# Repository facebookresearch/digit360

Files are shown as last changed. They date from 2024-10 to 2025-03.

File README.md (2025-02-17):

# Digit 360
##### Unlocking new capabilities, and enabling future research on the nature of touch.

<p align="center">
<sub>Mike Lambeta, Tingfan Wu,
Ali Sengül,
Victoria Rose Most,
Nolan Black,
Kevin Sawyer,
Romeo Mercado,
Haozhi Qi,
Chaithanya Krishna Bodduluri,
Alexander Sohn,
Byron Taylor,
Norb Tydingco,
Gregg Kammerer,
Dave Stroud,
Jake Khatha,
Kurt Jenkins,
Kyle Most,
Neal Stein,
Ricardo Chavira,
Thomas Craven-Bartle,
Eric Sanchez,
Yitian Ding,
Jitendra Malik,
Roberto Calandra</sub>
</p>

<p align="center">
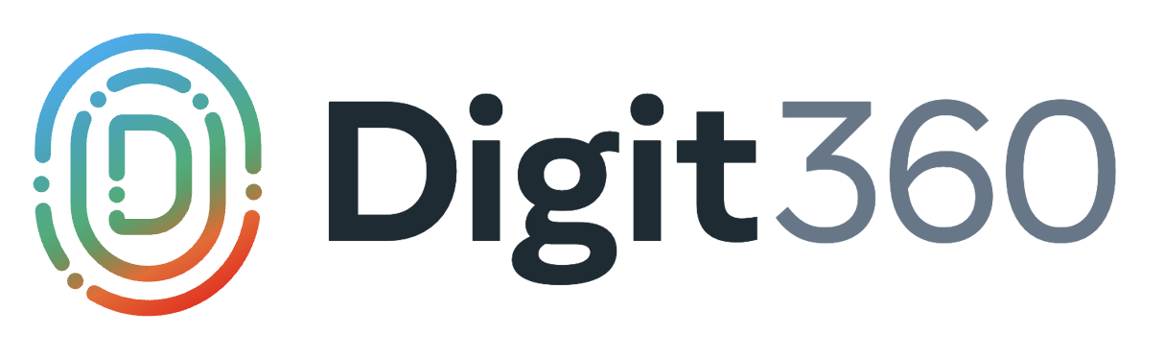
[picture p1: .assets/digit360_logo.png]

</p>

<p align="center">
    
    
    <!-- <a href=""><img src="http://img.shields.io/badge/Video-Link-green.svg"></img></a> -->
    
</p>

Digit 360 is a modular platform which provides rich, multi-modal digital touch-sensing capabilities through a hemispherical compliant embodiment. Digit 360 contains high-resolution sensors (~8.3 million taxels) that respond to omnidirectional touch, capture multi-modal signals, and use on-device artificial intelligence to process the data in real time.

<p align="center">
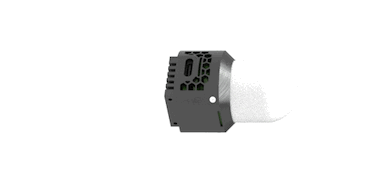
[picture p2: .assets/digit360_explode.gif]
animated

</p>

## Call for Proposals

AI Research at Meta, in partnership with GelSight Inc., invites proposals from universities and research organizations interested in using the next generation touch sensor Digit 360 to accelerate research, drive open source development, and contribute to the open source community. Fully assembled Digit 360’s will be made available at no charge to researchers that will make rigorous and creative use of the sensor in existing or planned research projects. 

Apply for the [Call for Proposals](https://digit.ml/cfp).

## Digit 360 Overview

The full description of the research methods is found in the [Digit 360 paper](https://ai.facebook.com/research/publications/digitizing-touch-with-an-artificial-multimodal-fingertip)

<p align="center">
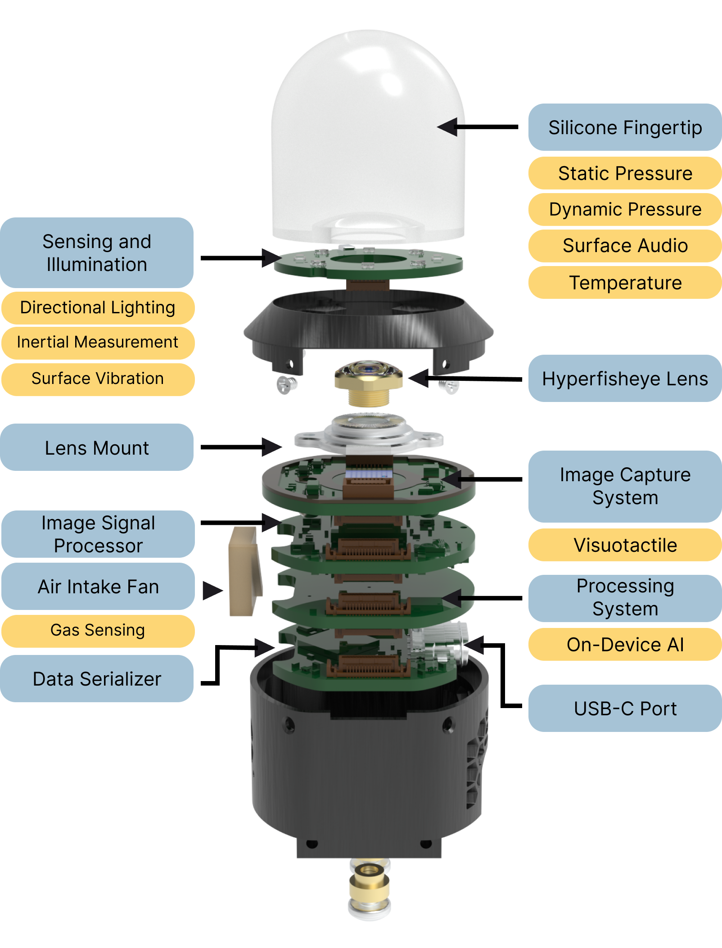
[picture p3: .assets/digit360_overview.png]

</p>

## Digit 360 Design

Digit 360 is composed of a 5 printed circuit board (PCB) stack with a 2 part mechanical housing, a custom hyperfisheye lens, and an artificial fingertip. 

See the design guidelines and design files [README](./design/README.md) for additional information.

## 🛠️ Installation

Please follow the instructions in [this doc](./digit360/README.md) to set up the environment and build the ROS2 package.

## 💻 Setup

We provide two methods for interacting with the Digit 360 devices. 

#### 1. [Standalone Package](./digit360/interface)

It provides python interface for accessing modalities output by digit360. Run the following command to test:
```
python digit360/interface/examples/test_usb.py
```

#### 2. [ROS2 Package](./digit360/ros2)

It provides ros2 interface to publish different modalities output by digit360. Run the following command to test:

```commandline
ros2 launch d360 d360_min_launch.py
```

## RL Environments and Simulation

To facilitate reinforcement learning environments, we provide a set of sectorized and convex meshes described in URDF formats found in the [meshes](./meshes/) folder.

<p align="center">
animated
animated

Both convex and sectorized meshes can be imported into [IsaacSim](https://developer.nvidia.com/isaac/sim).
</p>

## 💡 Multimodal Classification

We provide an example on how to run material / action classifications on touch interactions using the Digit 360.

Please check out [this doc](train/multimodal/README.md) for the detailed instructions.

## Related Works using Digit 360

* [In-Hand Object Rotation via Rapid Motor Adaptation, Haozhi Qi et al.](https://haozhi.io/hora/)
* [General In-Hand Object Rotation with Vision and Touch, Haozhi Qi et al.](https://haozhi.io/rotateit/)

## 📚 Citing Digit 360

If you find this repository useful, please consider giving a star :star: and citation:

```
@inproceedings{lambeta2024digit360,
    title={Digitizing Touch with an Artificial Multimodal Fingertip},
    author={Mike Lambeta, Tingfan Wu, Ali Sengul, Victoria Rose Most, Nolan Black, Kevin Sawyer, Romeo Mercado, Haozhi Qi, Alexander Sohn, Byron Taylor, Norb Tydingco, Gregg Kammerer, Dave Stroud, Jake Khatha, Kurt Jenkins, Kyle Most, Neal Stein, Ricardo Chavira, Thomas Craven-Bartle, Eric Sanchez, Yitian Ding, Jitendra Malik, Roberto Calandra},
    booktitle = {arXiv},
    year = {2024}
}
```

## License
This project is licensed under [LICENSE](LICENSE).

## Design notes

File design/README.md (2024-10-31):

# Digit 360 Design Guidelines

## Fingertip Design and Molds

The fingetip design is included for customization, which allows for alternative shapes of the hemispherical volume providing that the interface to the Digit 360 fingertip [gelsensor](./hardware/templates/gelsensor/) base is used. 

Mold designs can be 3D printed or CNC machined using 6061 aluminum.

* [Mold Design Files](./fingertip/digit360_fingertip_mold.stp)
* [Fingertip Design Files](./fingertip/digit360_fingertip.stp)

## Hardware

Hardware schematics and guidelines for manufacturing are found [here](./hardware/)

## Mechanical

The full Digit 360 design is provided as a `step` file [here](./mechanical/digit360.stp)

## Digit 360 Hyperfisheye Lens

Two custom lenses are designed specficially to highlight features important to visuotactile capture. The Digit 360 lenses can be manufacutred by single point diamond turning (SPDT) or injection molding techniques.

#### [Injection Molded Lens](digit360_lens.stp)
* With each element exposed in the [elements](./elements/) folder.

#### [SPDT Lens](./spdt/digit360_spdt_lens.STEP)

<p align="center">
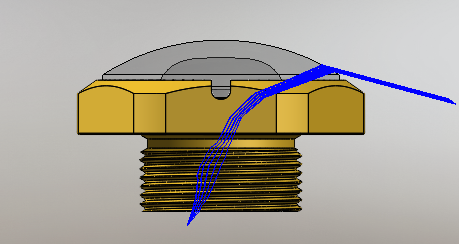
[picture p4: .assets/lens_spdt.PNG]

</p>

See the [CONTRIBUTING](CONTRIBUTING.md) file for how to help out.

## License
Digit 360 is Attribution-NonCommercial 4.0 International licensed, as found in the [LICENSE](LICENSE) file.

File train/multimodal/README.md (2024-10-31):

# Multimodal Classification for Digit360

We provide instructions on how to run multimodal classification experiments provided in our paper.

Install conda environment and torch
```
conda create -n d360
conda activate d360
conda install pytorch torchvision torchaudio pytorch-cuda=11.8 -c pytorch -c nvidia -y
```

We will also use foxglove to get the data:
```
pip install mcap-protobuf-support==0.0.10 mcap-ros2-support==0.1.0 mcap-ros1-support==0.4.0 
pip install foxglove-data-platform==0.6.0 duckdb ipympl 
pip install tensorboardX tyro opencv-python
```

Generate Data. It fetches foxglove data to `data/` folder.

```
python tools/gen_data_from_foxglove.py
```

Then one can run modality according to the following example script:
```
python train.py --data-path data/cls --rgb --output output_rgb
python train.py --data-path data/cls --imu --output output_imu
python train.py --data-path data/cls --mic --output output_mic  # simple vector form
python train.py --data-path data/cls --specgram --output output_specgram
```

To run experiments with multiple modalities, simply append the arguments together
```
CUDA_VISIBLE_DEVICES=0 python train.py --data-path data/cls --rgb --imu --mic --specgram --output output_name
```

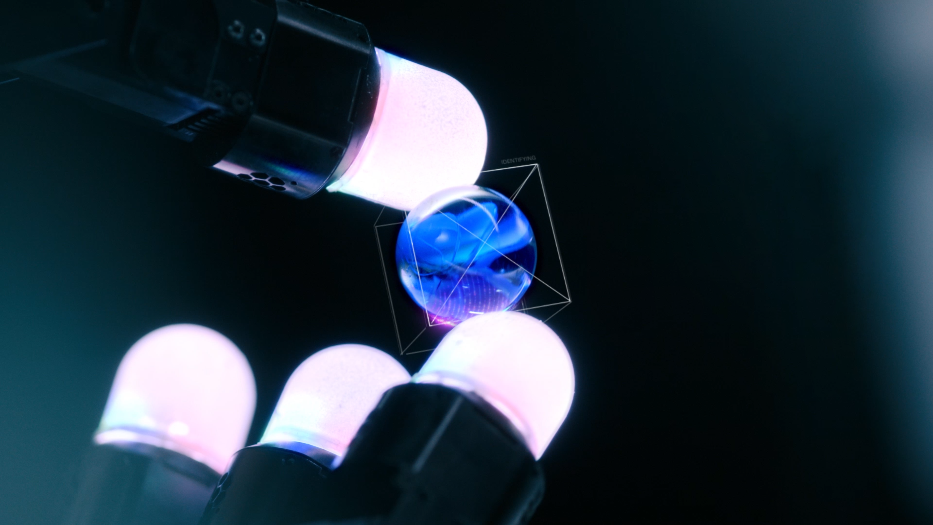
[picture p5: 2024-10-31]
.assets/digit360_hand.png

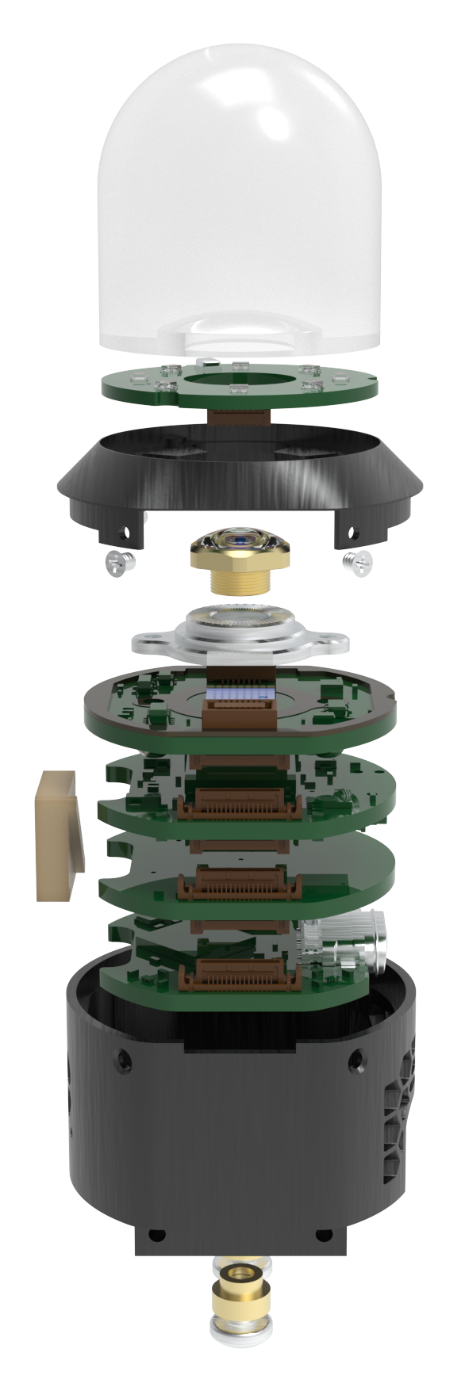
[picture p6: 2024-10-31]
.assets/digit_360_expand.50.png

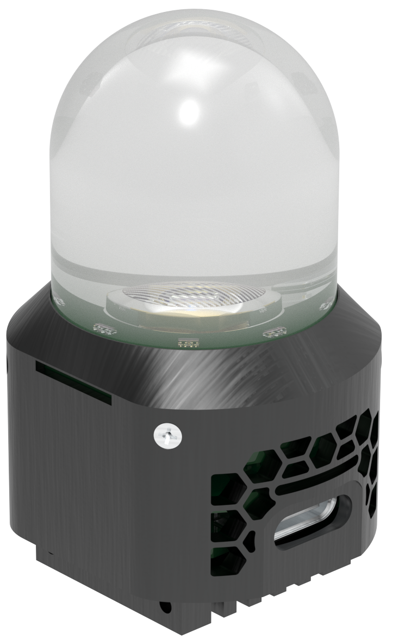
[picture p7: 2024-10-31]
.assets/digit_360_full_keyshot.46.png

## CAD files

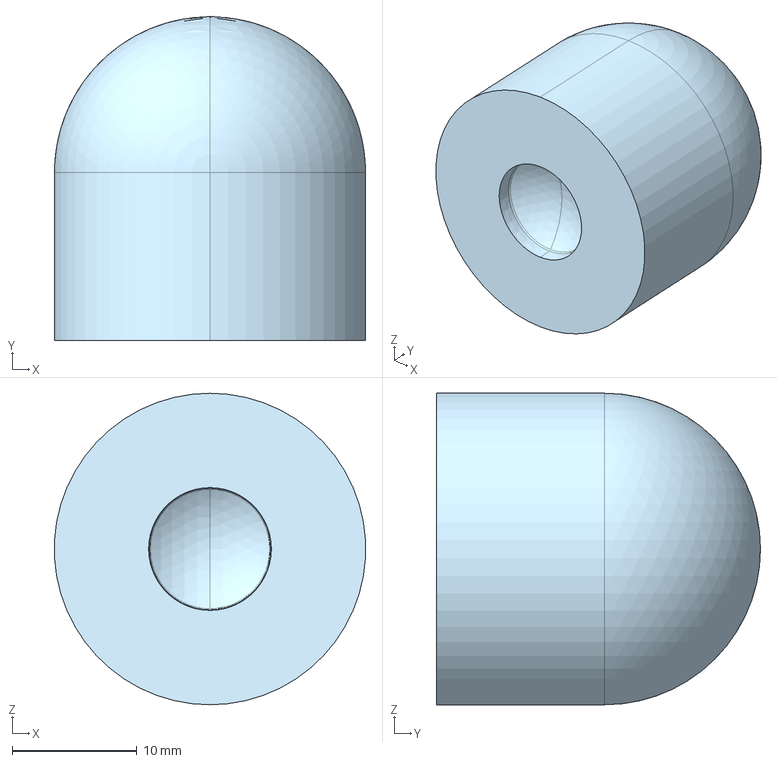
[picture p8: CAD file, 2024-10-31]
design/fingertip/digit360_fingertip.stp
25.0 x 26.0 x 25.0 mm

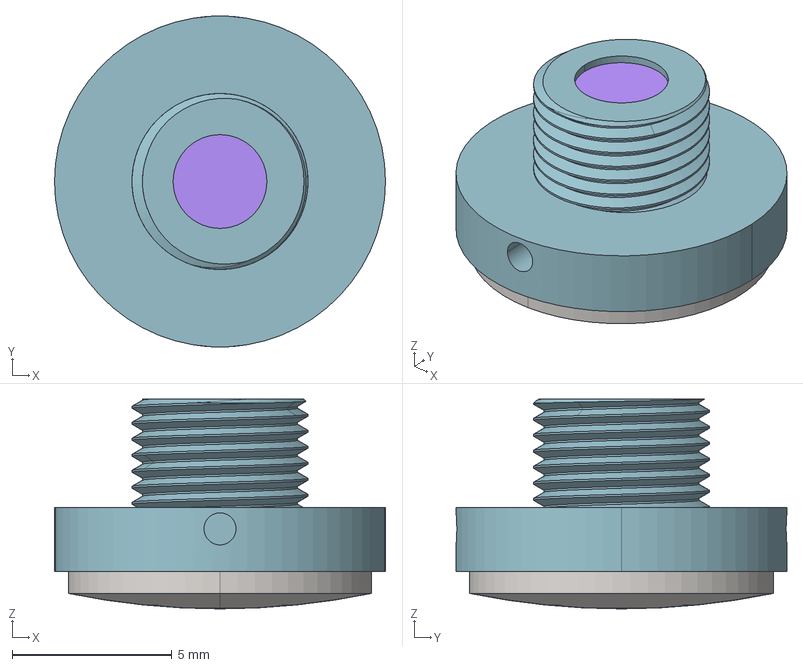
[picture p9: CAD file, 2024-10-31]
design/lens/digit360_lens.stp
10.3 x 10.3 x 6.56 mm
P0844246-03-HOUSING
P0844250-02-ELEMENT_1
P0844252-02-ELEMENT_2
P0844253-02-STOP_1
P0844253-02-STOP_2
P0844256-02-ELEMENT_3
P0844259-02-ELEMENT_4
P0844260-02-ELEMENT_5
P0843987-01-HYPERFISHEYE_LENS_2
P0844261-02-FILTER_GLASS
P0844613-01-ADHESIVE x 2

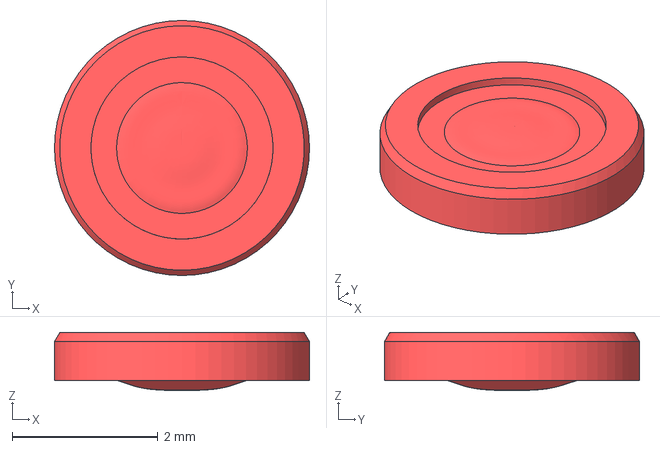
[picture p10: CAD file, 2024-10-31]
design/lens/elements/digit360_lens_L 5.stp
3.50 x 3.50 x 0.8 mm

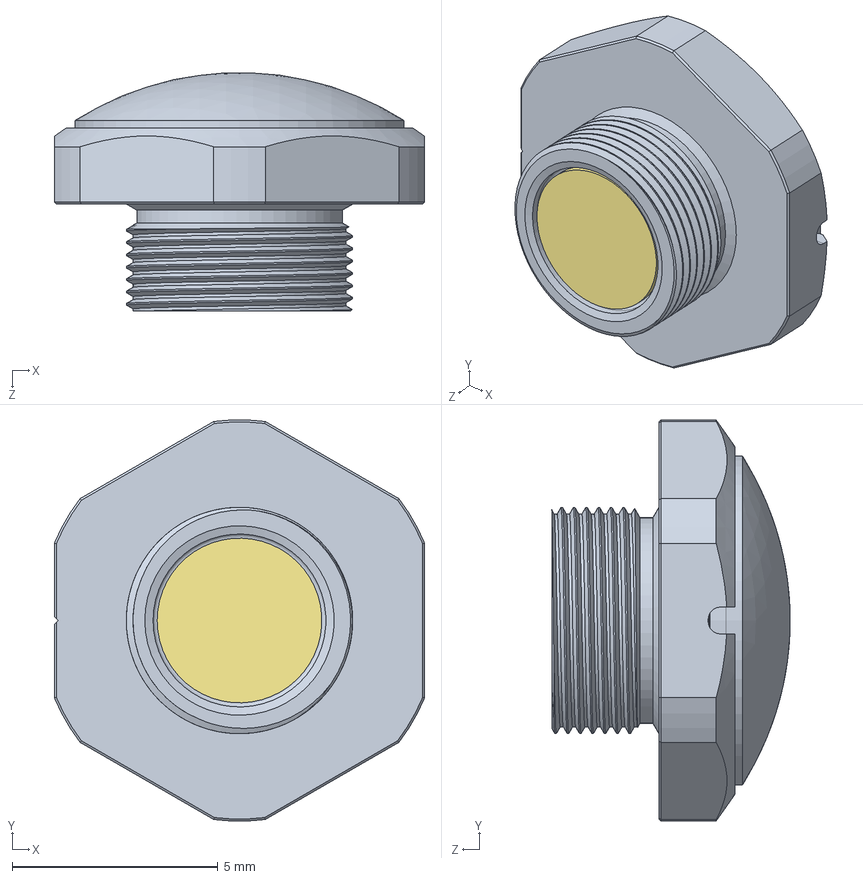
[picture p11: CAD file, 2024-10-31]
design/lens/spdt/digit360_spdt_lens.STEP
9.00 x 9.74 x 5.79 mm
647-06897-00_modified20211217

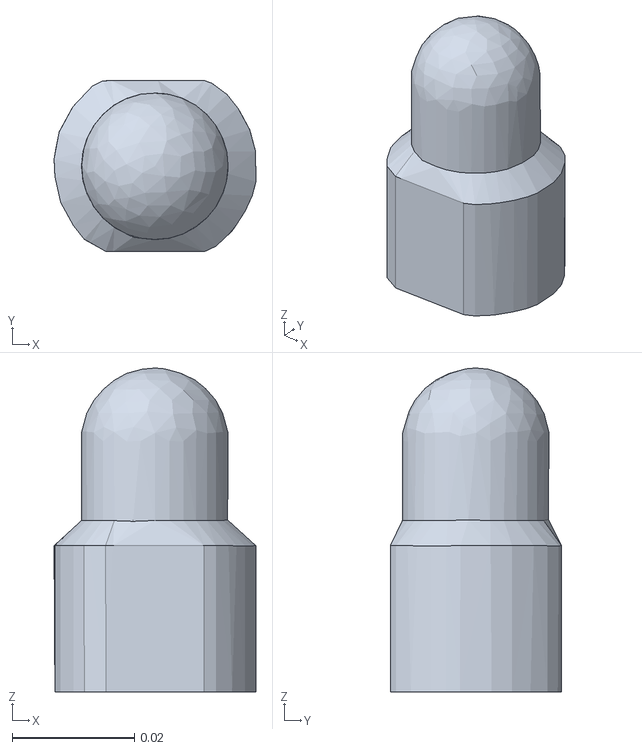
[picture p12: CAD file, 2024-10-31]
meshes/digit360_mesh.stl
0.033 x 0.028 x 0.053

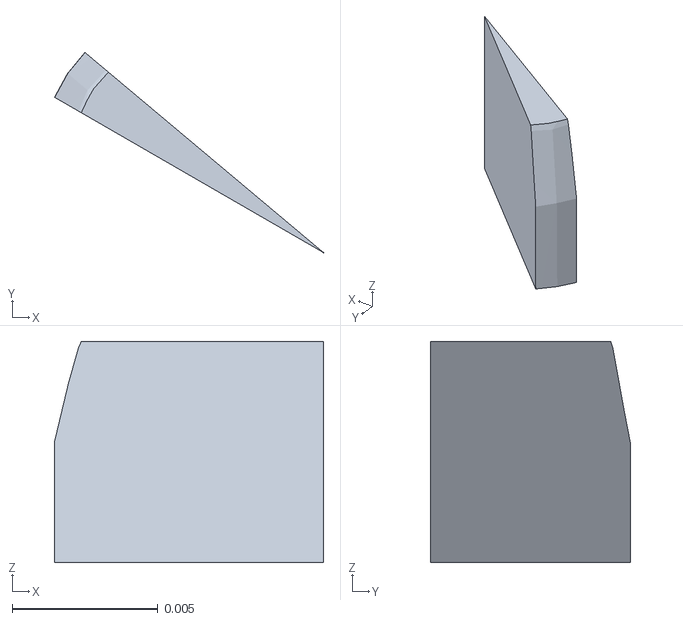
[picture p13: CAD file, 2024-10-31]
meshes/discrete/digit2_sensor_2l14.stl
0.00924 x 0.00688 x 0.0076

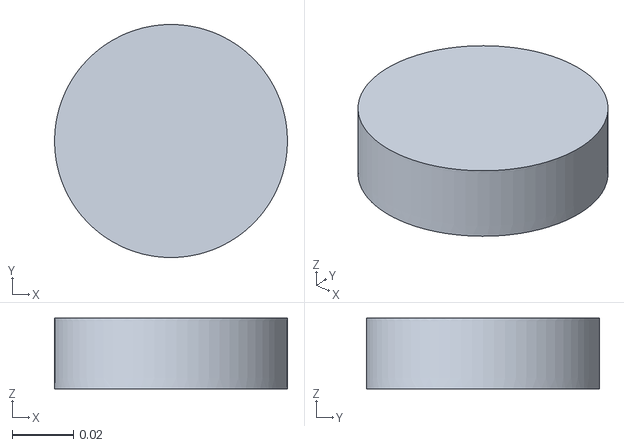
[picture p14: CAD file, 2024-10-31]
meshes/mounts/allegro_mount.stl
0.076 x 0.076 x 0.023

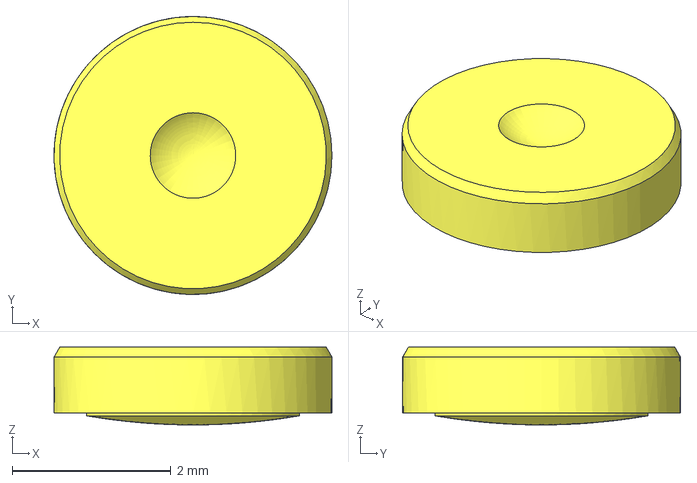
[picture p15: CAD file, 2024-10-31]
design/lens/elements/digit360_lens_L 2.stp
3.50 x 3.50 x 0.981 mm

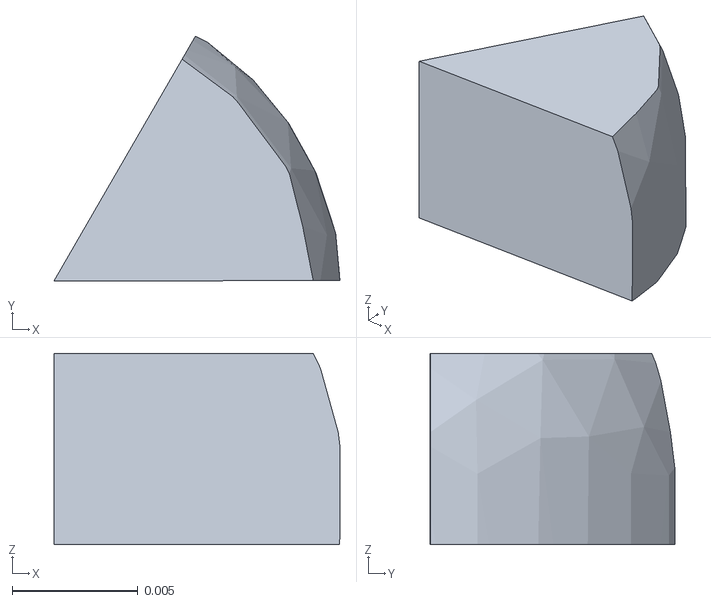
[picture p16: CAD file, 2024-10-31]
meshes/discrete/digit2_sensor_2l0.stl
0.0114 x 0.00972 x 0.0076

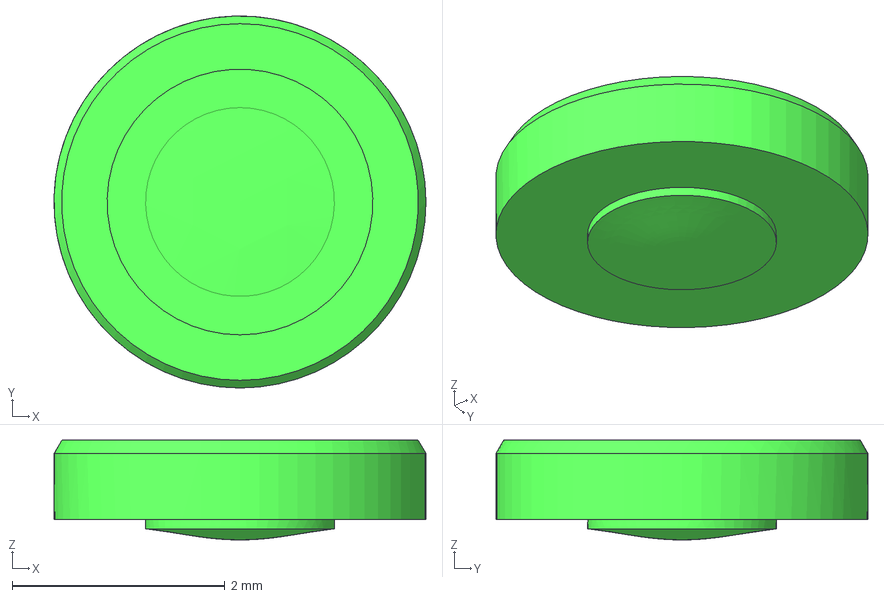
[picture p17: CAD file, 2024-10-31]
design/lens/elements/digit360_lens_L 4.stp
3.50 x 3.50 x 0.94 mm

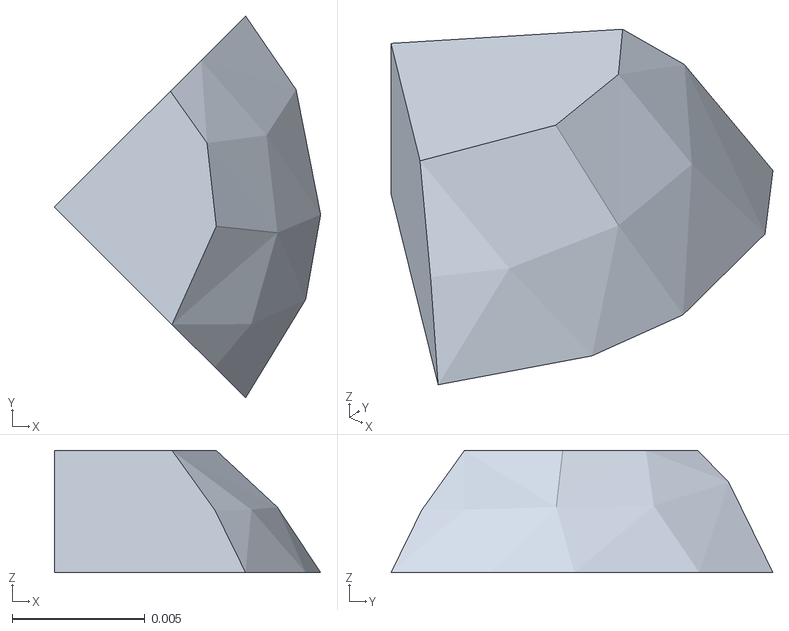
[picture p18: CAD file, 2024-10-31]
meshes/discrete/digit2_sec4_sensor_3l3.stl
0.01 x 0.0144 x 0.0046

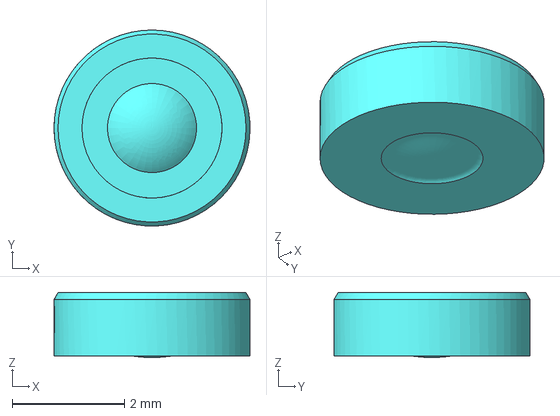
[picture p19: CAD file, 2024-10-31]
design/lens/elements/digit360_lens_L 3.stp
3.50 x 3.50 x 1.16 mm

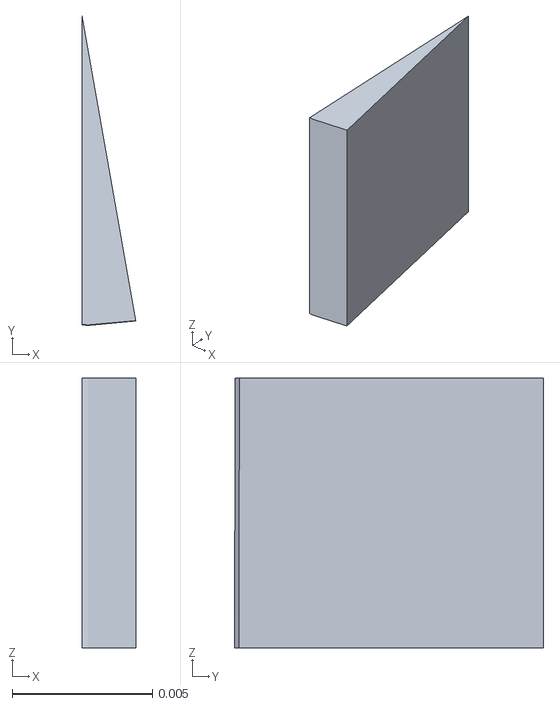
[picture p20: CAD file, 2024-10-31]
meshes/discrete/digit2_sensor_1l27.stl
0.00191 x 0.011 x 0.0096

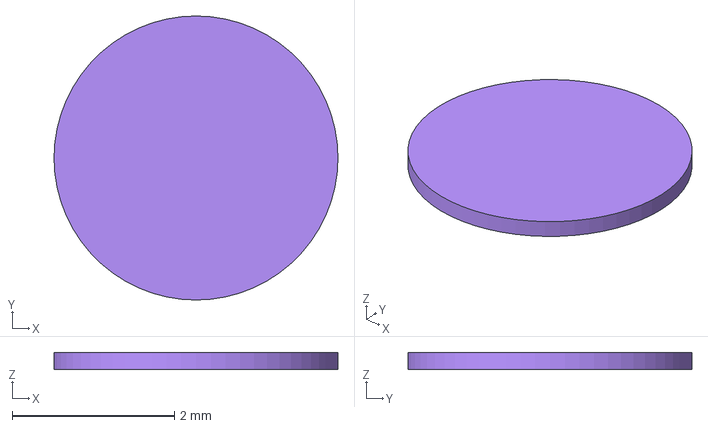
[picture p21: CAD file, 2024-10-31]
design/lens/elements/digit360_lens_filter.stp
3.50 x 3.50 x 0.21 mm

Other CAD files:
meshes/discrete/digit2_sensor_3l32.stl
design/lens/elements/digit360_lens_Stop.stp
meshes/discrete/digit2_sensor_1l25.stl
design/lens/elements/digit360_lens_L 1.stp
design/lens/elements/digit360_lens_adhesive.stp
meshes/discrete/base_link.STL
meshes/discrete/base_link_left.STL
meshes/discrete/box.stl
meshes/discrete/box.stl.convex.stl
meshes/discrete/digit.STL
meshes/discrete/digit.STL.convex.stl
meshes/discrete/digit2_sec4_sensor_1l0.stl
meshes/discrete/digit2_sec4_sensor_1l1.stl
meshes/discrete/digit2_sec4_sensor_1l2.stl
meshes/discrete/digit2_sec4_sensor_1l3.stl
meshes/discrete/digit2_sec4_sensor_2l0.stl
meshes/discrete/digit2_sec4_sensor_2l1.stl
meshes/discrete/digit2_sec4_sensor_2l2.stl
meshes/discrete/digit2_sec4_sensor_2l3.stl
meshes/discrete/digit2_sec4_sensor_3l0.stl
meshes/discrete/digit2_sec4_sensor_3l1.stl
meshes/discrete/digit2_sec4_sensor_3l2.stl
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

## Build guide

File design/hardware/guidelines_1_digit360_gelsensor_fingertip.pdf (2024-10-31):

A

B

C

D

E

1 | 1

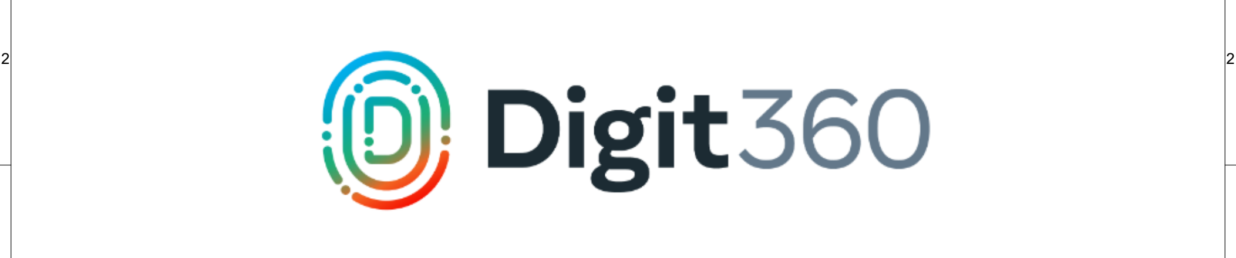
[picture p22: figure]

3 | 3
4 | 4
Copyright (c) Meta Platforms, Inc. and affiliates.
All rights reserved.
This source code is licensed under the license found in the LICENSE file in the root directory of this source tree.

# Digit 360 GelSensor Fingertip

1 | 1
2 | 2
3 | 3
4 | 4

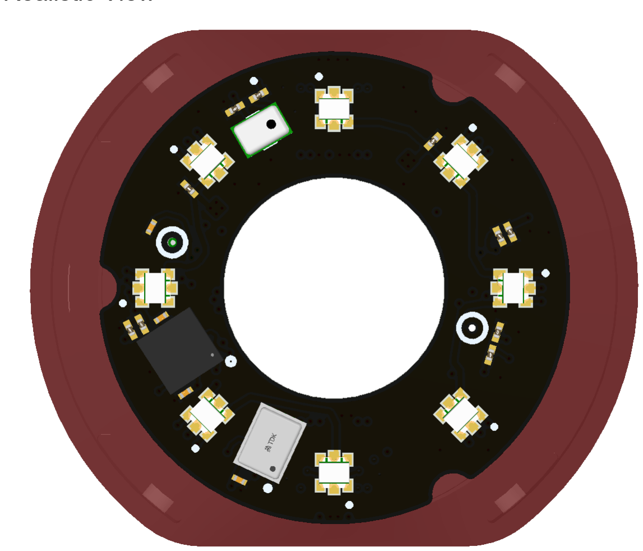
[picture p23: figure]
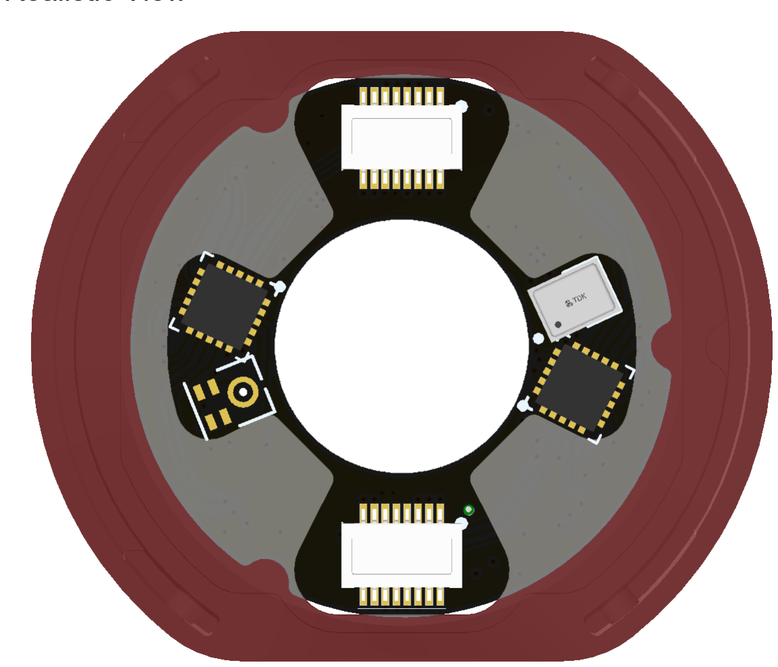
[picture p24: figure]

Realistic View | Realistic View

1 | 1
2 | 2
3 | 3
4 | 4

STACKUP SUMMARY:
A. NUMBER OF COPPER LAYERS: 6
B. BOARD THICKNESS SHALL BE 1.2mm +/- 10%
C. COPPER: See Layer Stack
D. DEFAULT TRACE/SPACE: 5mil / 5mil
E. CONDUCTOR WIDTH TOLERANCE = +/- 0.01mm

1.

SURFACE FINISH/PLATING:
A. BOARD SHALL BE IMMERSION GOLD PLATED (ENIG) ACCORDING TO IPC-4552. THICKNESS SHALL BE A MINIMUM OF 0.05μm GOLD OVER 3-6μm NICKEL

2.

SOLDERMASK WITH LIQUID PHOTO IMAGEABLE (LPI) PER IPC-SM-840C, CLASS T. COLOR: MATTE BLACK

3.

SILKSCREEN
COLOR: WHITE

4.

LOCATE MANUFACTURER'S IDENTIFICATION AND LOT CODE ON BOTTOM SIDE FREE FROM ALL METAL ENTITY RENDERED IN SILKSCREEN.

5.

DETAILS NOT SPECIFIED ARE AT MANUFACTURER'S OPTION BUT FINAL APPROVAL MUST BE OBTAINED

6.

7. FULLY ROUTE OUT EACH BOARD, NO TEETH OR MOUSEBITES

NOTES: UNITS IN MILLIMETERS UNLESS OTHERWISE SPECIFIED

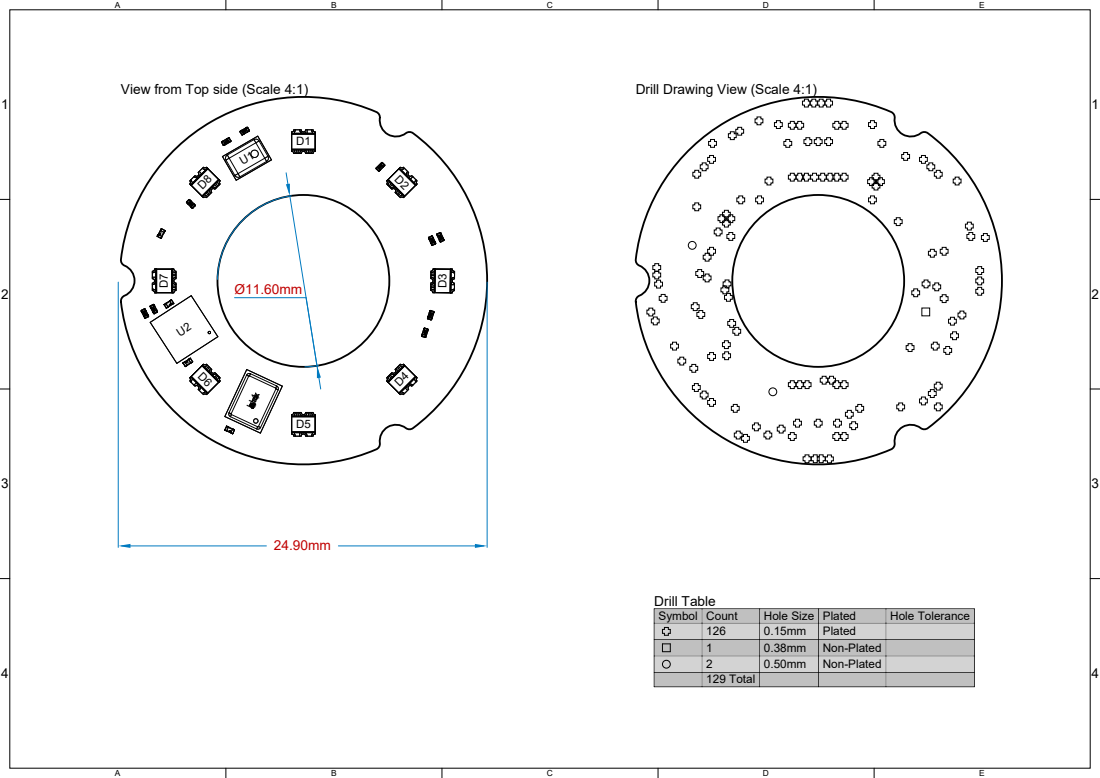
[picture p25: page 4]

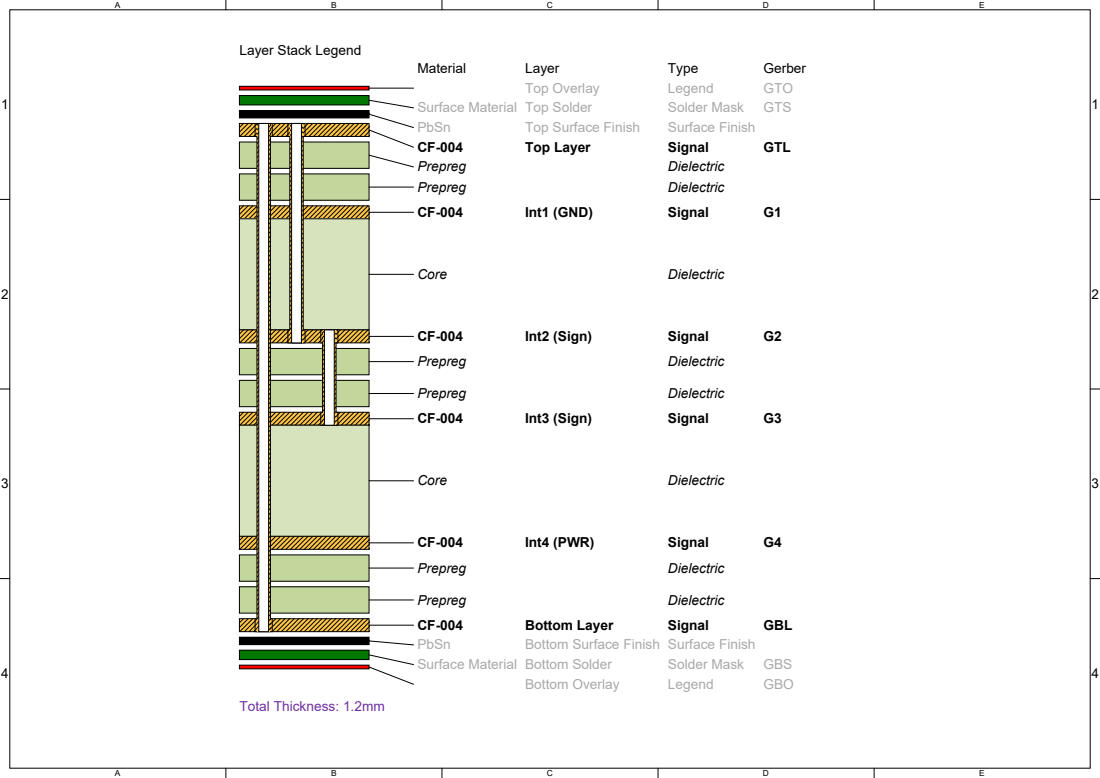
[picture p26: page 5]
Material; Layer; Type; Gerber; Top Overlay; Legend; GTO; Surface Material Top Solder; Solder Mask; GTS; PbSn; Top Surface Finish; Surface Finish; Top Layer; Signal; GTL; Prepreg; Dielectric; Int1 (GND); Core; Int2 (Sign); Int3 (Sign); Int4 (PWR); Bottom Layer; GBL; Bottom Surface Finish Surface Finish; Surface Material Bottom Solder; GBS; Bottom Overlay; GBO; Total Thickness: 1.2mm

Layer Stack Legend

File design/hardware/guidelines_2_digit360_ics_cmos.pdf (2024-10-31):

A

B

C

D

E

1 | 1

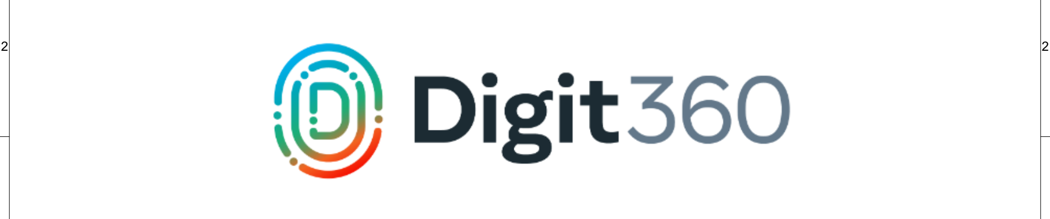
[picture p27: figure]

3 | 3
4 | 4

Copyright (c) Meta Platforms, Inc. and affiliates.
All rights reserved.
This source code is licensed under the license found in the LICENSE file in the root directory of this source tree.

# Digit 360 ICS CMOS

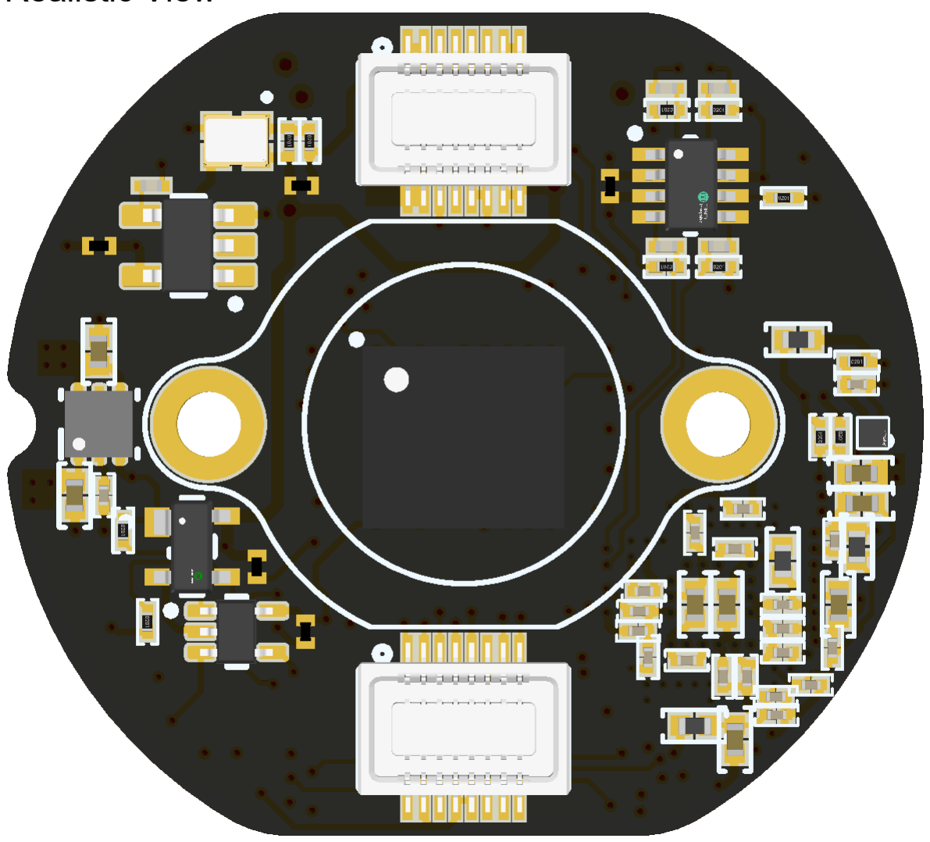
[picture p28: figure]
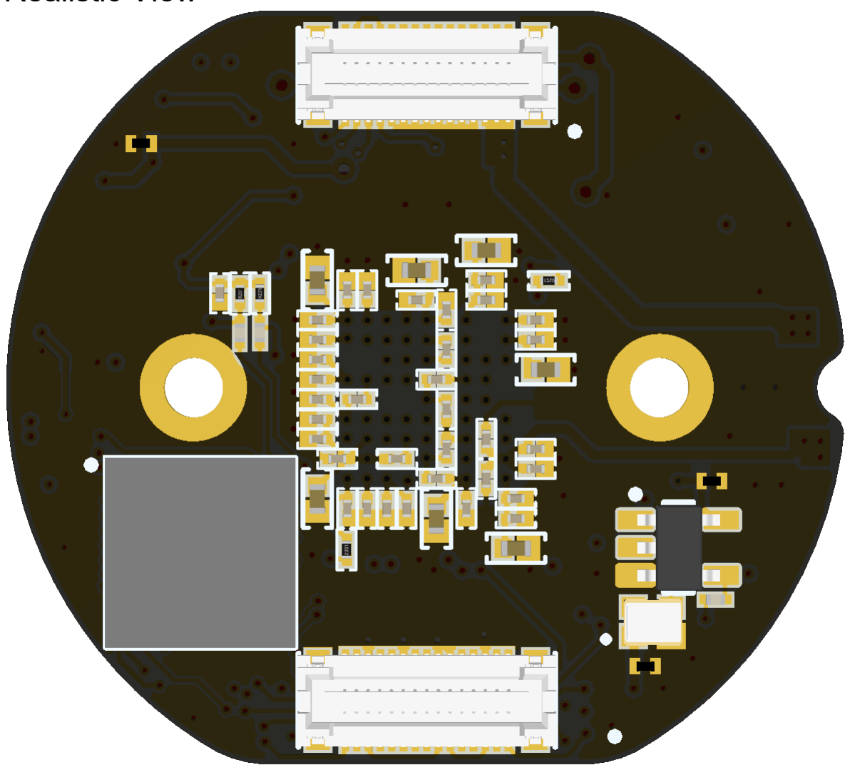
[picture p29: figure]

1 | 1
2 | 2
3 | 3
4 | 4
Realistic View | Realistic View

1 | 1
2 | 2
3 | 3
4 | 4
1. INTERPRET THIS DRAWING IN ACCORDANCE WITH IPC-D-325A
2. BOARD FABRICATION AND QUALITY PER IPC-6012, CLASS 2, EXCEPT SPECIFIED HEREIN
3. MUST COMPLY WITH EUROPEAN DIRECTIVE 2002/95/EC (RoHS)
4. DIMENSIONAL LIMITS APPLY AFTER PLATING OR COATING
5. BOW AND TWIST MAXIMUM IS 0.75%
MATERIAL: LAMINATE AND PREPREG SHALL BE IN ACCORDANCE WITH IPC-4101/21. 170 DEGREES CELSIUS MINIMUM Tg, UL 94V-0

6.

STACKUP SUMMARY:
A. NUMBER OF COPPER LAYERS: 6
B. BOARD THICKNESS SHALL BE 62mil +/- 10%
C. COPPER: See Layer Stack
D. DEFAULT TRACE/SPACE: 4mil / 4mil
E. CONDUCTOR WIDTH TOLERANCE = +/- 0.01mm

7.

VIPPO (VIA IN PAD PLATED OVER) PER IPC-6012, CURRENT REVISION, CLASS 2, AS STATED IN NOTE 2.
a. FILL AND CAP All 0.2mm VIA HOLES WITH NON-CONDUCTIVE EPOXY
b. FILL AND CAP VIAS MUST BE PLANARIZED

8.

SURFACE FINISH/PLATING:
A. BOARD SHALL BE IMMERSION GOLD PLATED (ENIG) ACCORDING TO IPC-4552. THICKNESS SHALL BE A MINIMUM OF 0.05μm GOLD OVER 3-6μm NICKEL

9.

SOLDERMASK WITH LIQUID PHOTO IMAGEABLE (LPI) PER IPC-SM-840C, CLASS T. COLOR: MATTE BLACK

10.

SILKSCREEN PER SUPPLIED ARTWORK WITH ORGANIC, NON-CONDUCTIVE, EPOXY INK. SILKSCREEN MAY BE TRIMMED OFF ANY SOLDERABLE ENTITY.
COLOR: WHITE

11.

100% BARE BOARD ELECTRICAL TEST TO BE DONE WITH REFERENCE TO SUPPLIED NETLIST

12.

LOCATE MANUFACTURER'S IDENTIFICATION AND LOT CODE ON PRIMARY SIDE FREE FROM ALL METAL ENTITY RENDERED IN SILKSCREEN.

13.

DIFFERENTIAL CONTROLLED IMPEDANCE REQUIRED ON BOARD.
SEE TABLE : DIFFERENTIAL CONTROLLED IMPEDANCE
SEE TABLE : SINGLE ENDED CONTROLLED IMPEDANCE

14.

DETAILS NOT SPECIFIED ARE AT MANUFACTURER'S OPTION BUT FINAL APPROVAL MUST BE OBTAINED

15.

NOTES: UNITS IN MILLIMETERS UNLESS OTHERWISE SPECIFIED

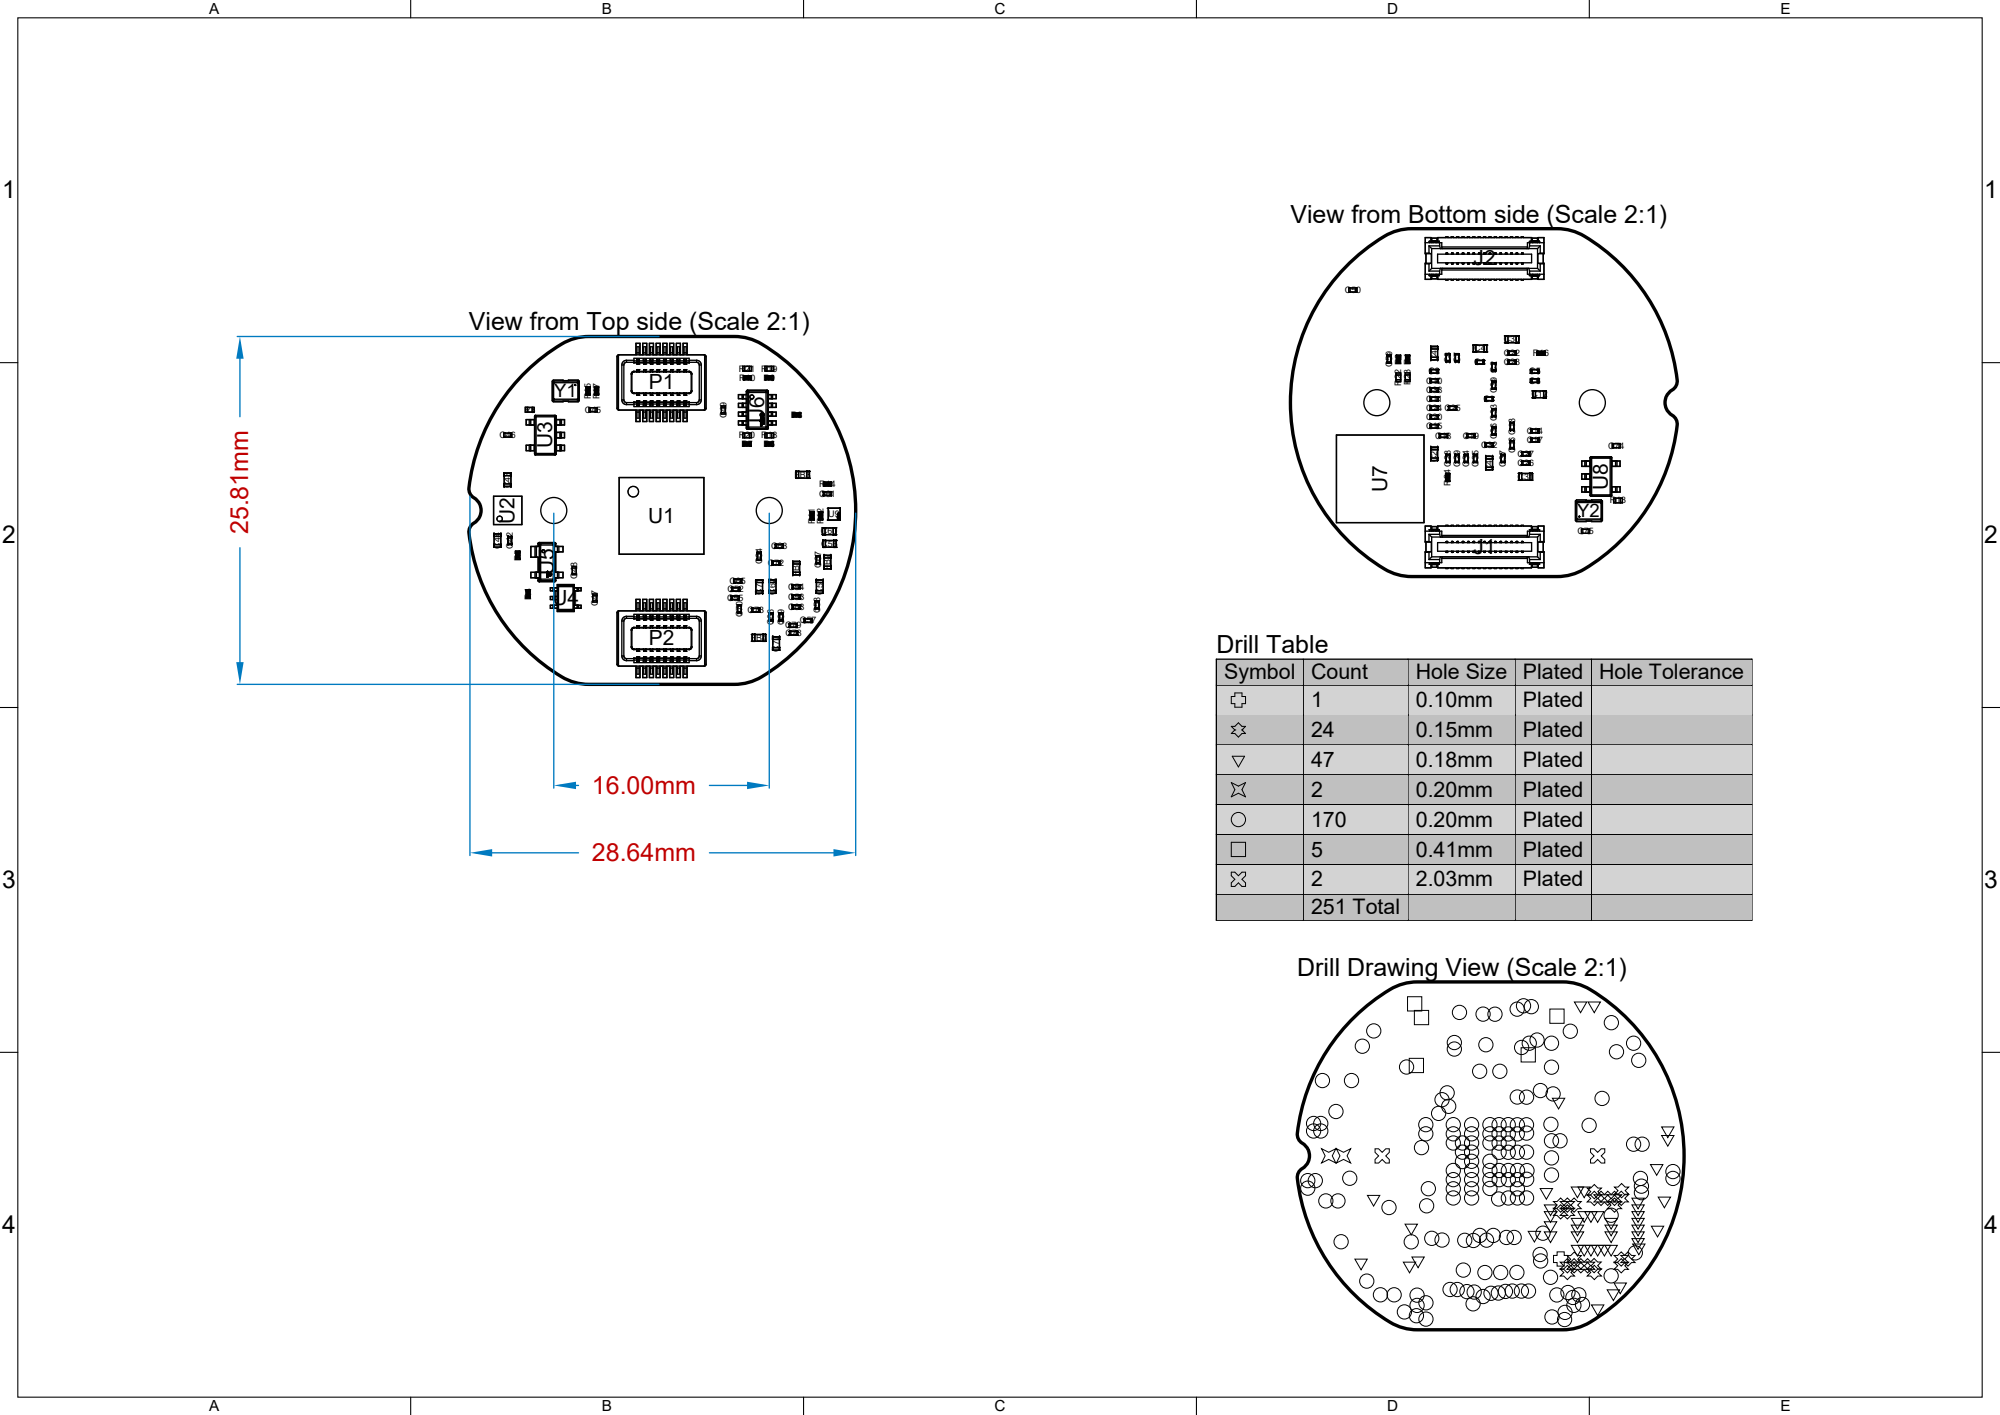
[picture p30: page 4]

View from Bottom side (Scale 2:1)

View from Top side (Scale 2:1)

Drill Drawing View (Scale 2:1)

# Stack-Up (or similar)

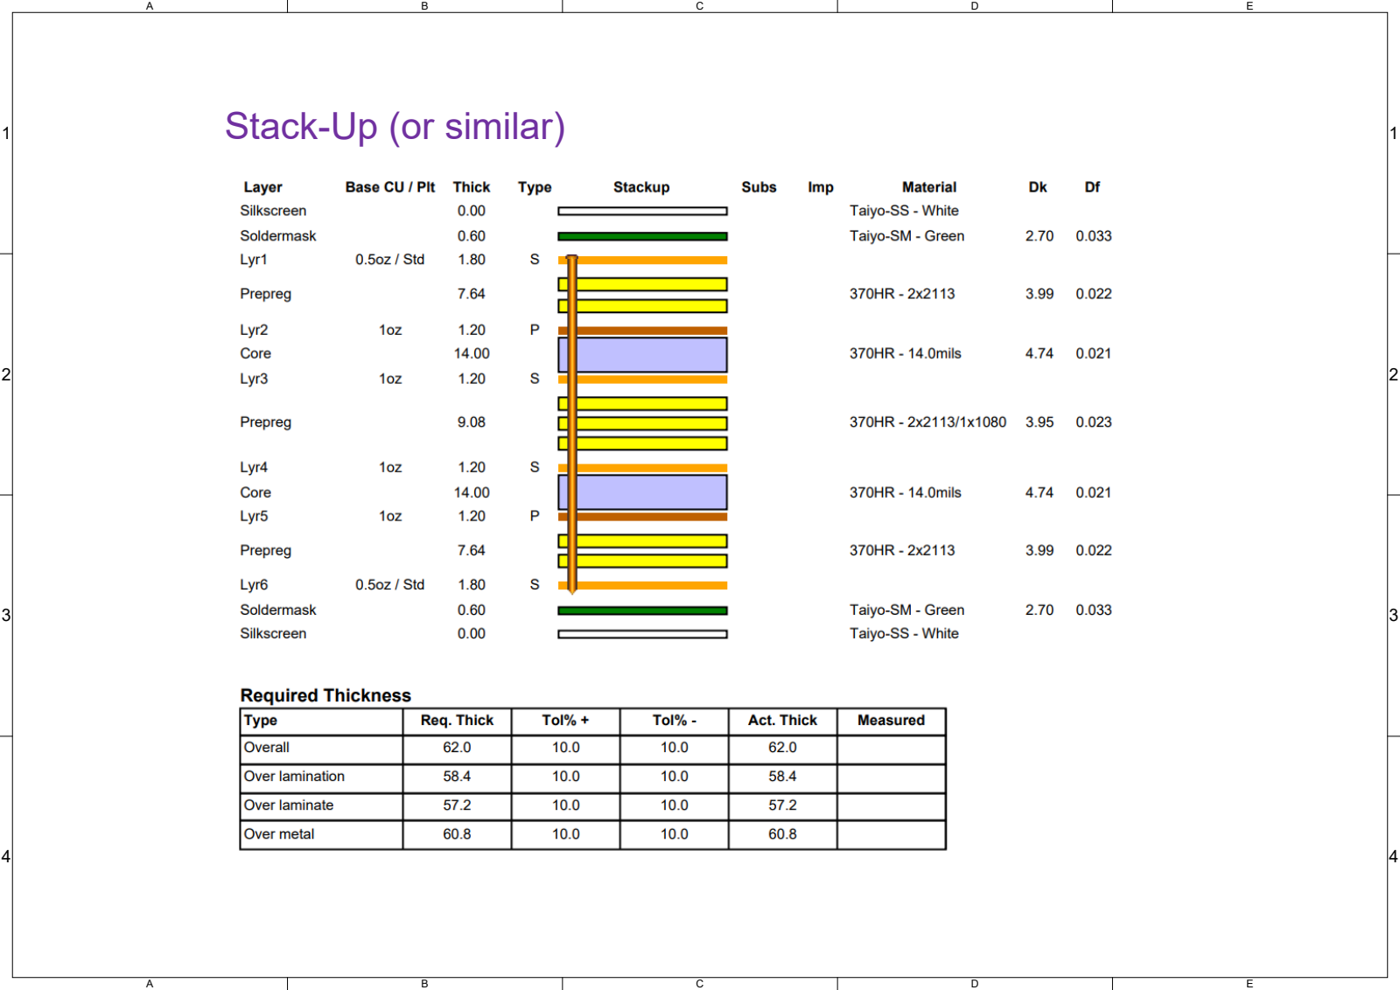
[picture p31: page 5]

1 | 1
2 | 2
3 | 3
4 | 4

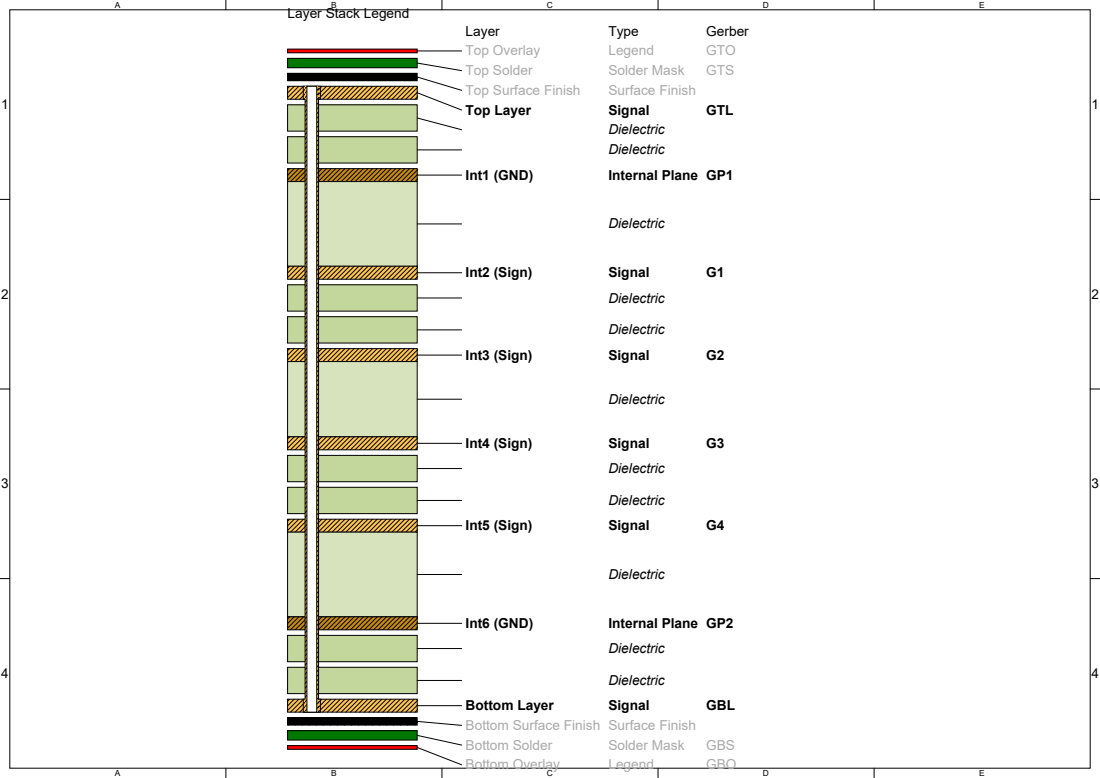
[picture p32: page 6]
Layer; Type; Gerber; Top Overlay; Legend; GTO; Top Solder; Solder Mask; GTS; Top Surface Finish; Surface Finish; Top Layer; Signal; GTL; Dielectric Dielectric; Int1 (GND); Internal Plane GP1; Dielectric; Int2 (Sign); Int3 (Sign); Int4 (Sign); Int5 (Sign); Int6 (GND); Internal Plane GP2; Bottom Layer; GBL; Bottom Solder; GBS; Bottom Overlay; GBO

Layer Stack Legend

Bottom Surface Finish Surface Finish

1 | 1
2 | 2
3 | 3
4 | 4

Target Impedance
100
100
100
100

Calculated Impedance
98.60
99.03
99.03
98.60

Trace layer
Top Layer
Int2 (Sign)
Int5 (Sign)
Bottom Layer

Wide Trace Width
5.00mil
4.00mil
4.00mil
5.00mil

Narrow Trace Width
5.00mil
4.00mil
4.00mil
5.00mil

Gap
5.00mil
9.00mil
9.00mil
5.00mil

Reference layers
Int1 (GND)
Int1 (GND),Int3 (Sign)
Int4 (Sign),Int6 (GND)
Int6 (GND)

Clearance
5.00mil
5.00mil
5.00mil
5.00mil

Target Tolerance
10%
10%
10%
10%

Transmission Line Structure Table

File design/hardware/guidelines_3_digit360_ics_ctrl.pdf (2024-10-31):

A

B

C

D

E

1 | 1


3 | 3
4 | 4

# Digit 360 ICS CTRL

Copyright (c) Meta Platforms, Inc. and affiliates.
All rights reserved.
This source code is licensed under the license found in the LICENSE file in the root directory of this source tree.

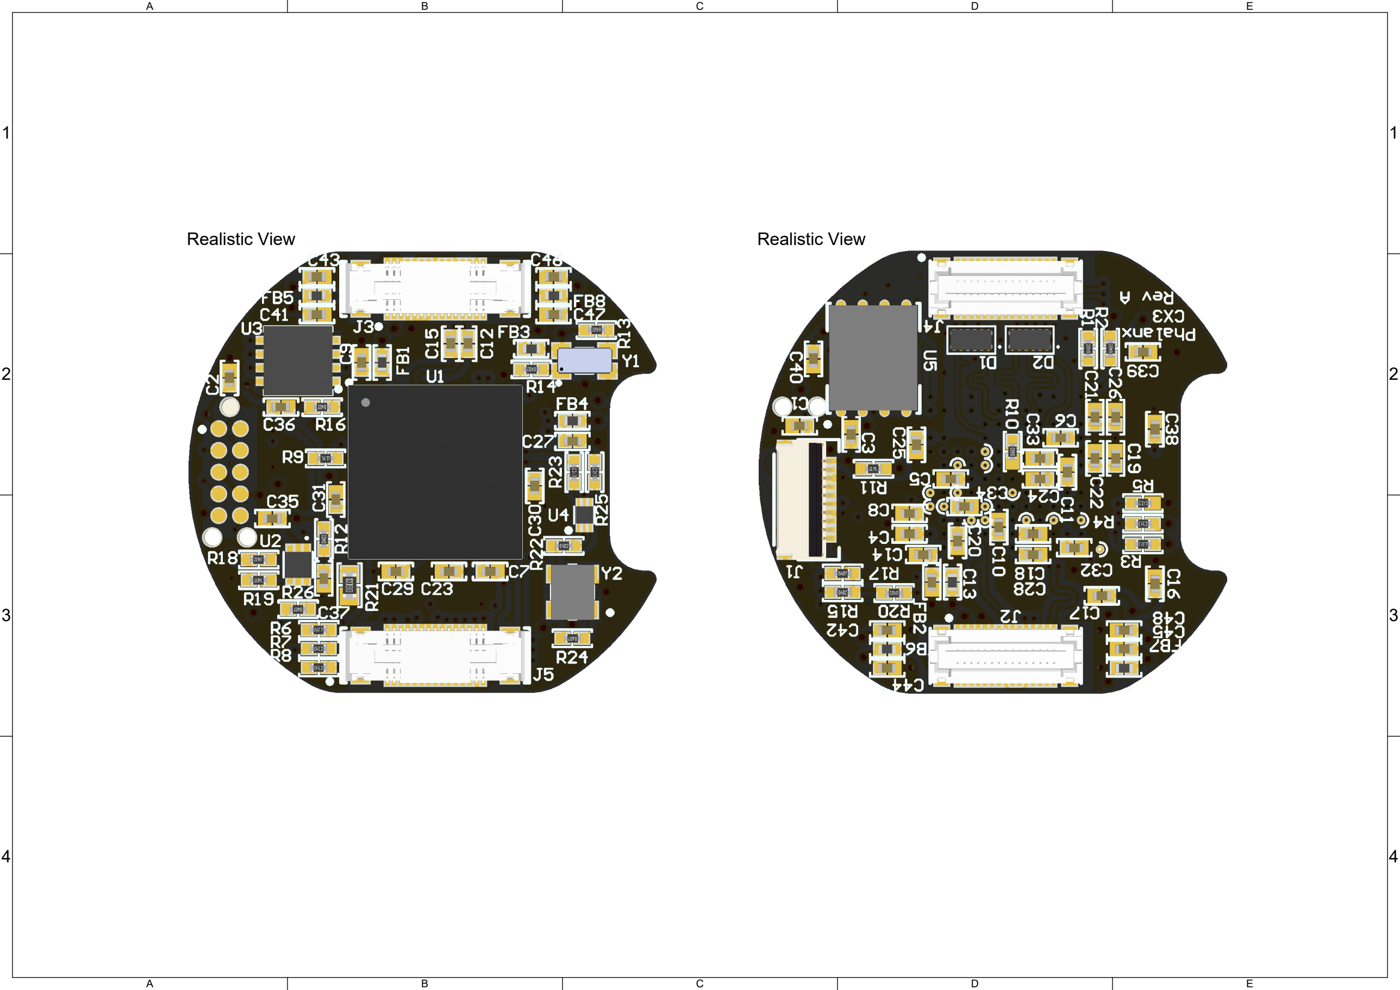
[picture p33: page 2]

1 | 1
2 | 2
3 | 3
4 | 4
Realistic View | Realistic View

1 | 1
2 | 2
3 | 3
4 | 4
1. INTERPRET THIS DRAWING IN ACCORDANCE WITH IPC-D-325A
2. BOARD FABRICATION AND QUALITY PER IPC-6012, CLASS 2, EXCEPT SPECIFIED HEREIN
3. MUST COMPLY WITH EUROPEAN DIRECTIVE 2002/95/EC (RoHS)
4. DIMENSIONAL LIMITS APPLY AFTER PLATING OR COATING
5. BOW AND TWIST MAXIMUM IS 0.75%
MATERIAL: LAMINATE AND PREPREG SHALL BE IN ACCORDANCE WITH IPC-4101/21. 170 DEGREES CELSIUS MINIMUM Tg, UL 94V-0

6.

STACKUP SUMMARY:
A. NUMBER OF COPPER LAYERS: 8
B. BOARD THICKNESS SHALL BE 62mil +/- 10%
C. COPPER: See Layer Stack
D. DEFAULT TRACE/SPACE: 5mil / 5mil
E. CONDUCTOR WIDTH TOLERANCE = +/- 0.01mm

7.

VIPPO (VIA IN PAD PLATED OVER) PER IPC-6012, CURRENT REVISION, CLASS 2, AS STATED IN NOTE 2.
a. FILL AND CAP All 0.2mm VIA HOLES WITH NON-CONDUCTIVE EPOXY
b. FILL AND CAP VIAS MUST BE PLANARIZED

8.

SURFACE FINISH/PLATING:
A. BOARD SHALL BE IMMERSION GOLD PLATED (ENIG) ACCORDING TO IPC-4552. THICKNESS SHALL BE A MINIMUM OF 0.05μm GOLD OVER 3-6μm NICKEL

9.

SOLDERMASK WITH LIQUID PHOTO IMAGEABLE (LPI) PER IPC-SM-840C, CLASS T. COLOR: MATTE BLACK

10.

SILKSCREEN PER SUPPLIED ARTWORK WITH ORGANIC, NON-CONDUCTIVE, EPOXY INK. SILKSCREEN MAY BE TRIMMED OFF ANY SOLDERABLE ENTITY.
COLOR: WHITE

11.

100% BARE BOARD ELECTRICAL TEST TO BE DONE WITH REFERENCE TO SUPPLIED NETLIST

12.

LOCATE MANUFACTURER'S IDENTIFICATION AND LOT CODE ON PRIMARY SIDE FREE FROM ALL METAL ENTITY RENDERED IN SILKSCREEN.

13.

DIFFERENTIAL CONTROLLED IMPEDANCE REQUIRED ON BOARD.
SEE TABLE : DIFFERENTIAL CONTROLLED IMPEDANCE
SEE TABLE : SINGLE ENDED CONTROLLED IMPEDANCE

14.

DETAILS NOT SPECIFIED ARE AT MANUFACTURER'S OPTION BUT FINAL APPROVAL MUST BE OBTAINED

15.

NOTES: UNITS IN MILLIMETERS UNLESS OTHERWISE SPECIFIED

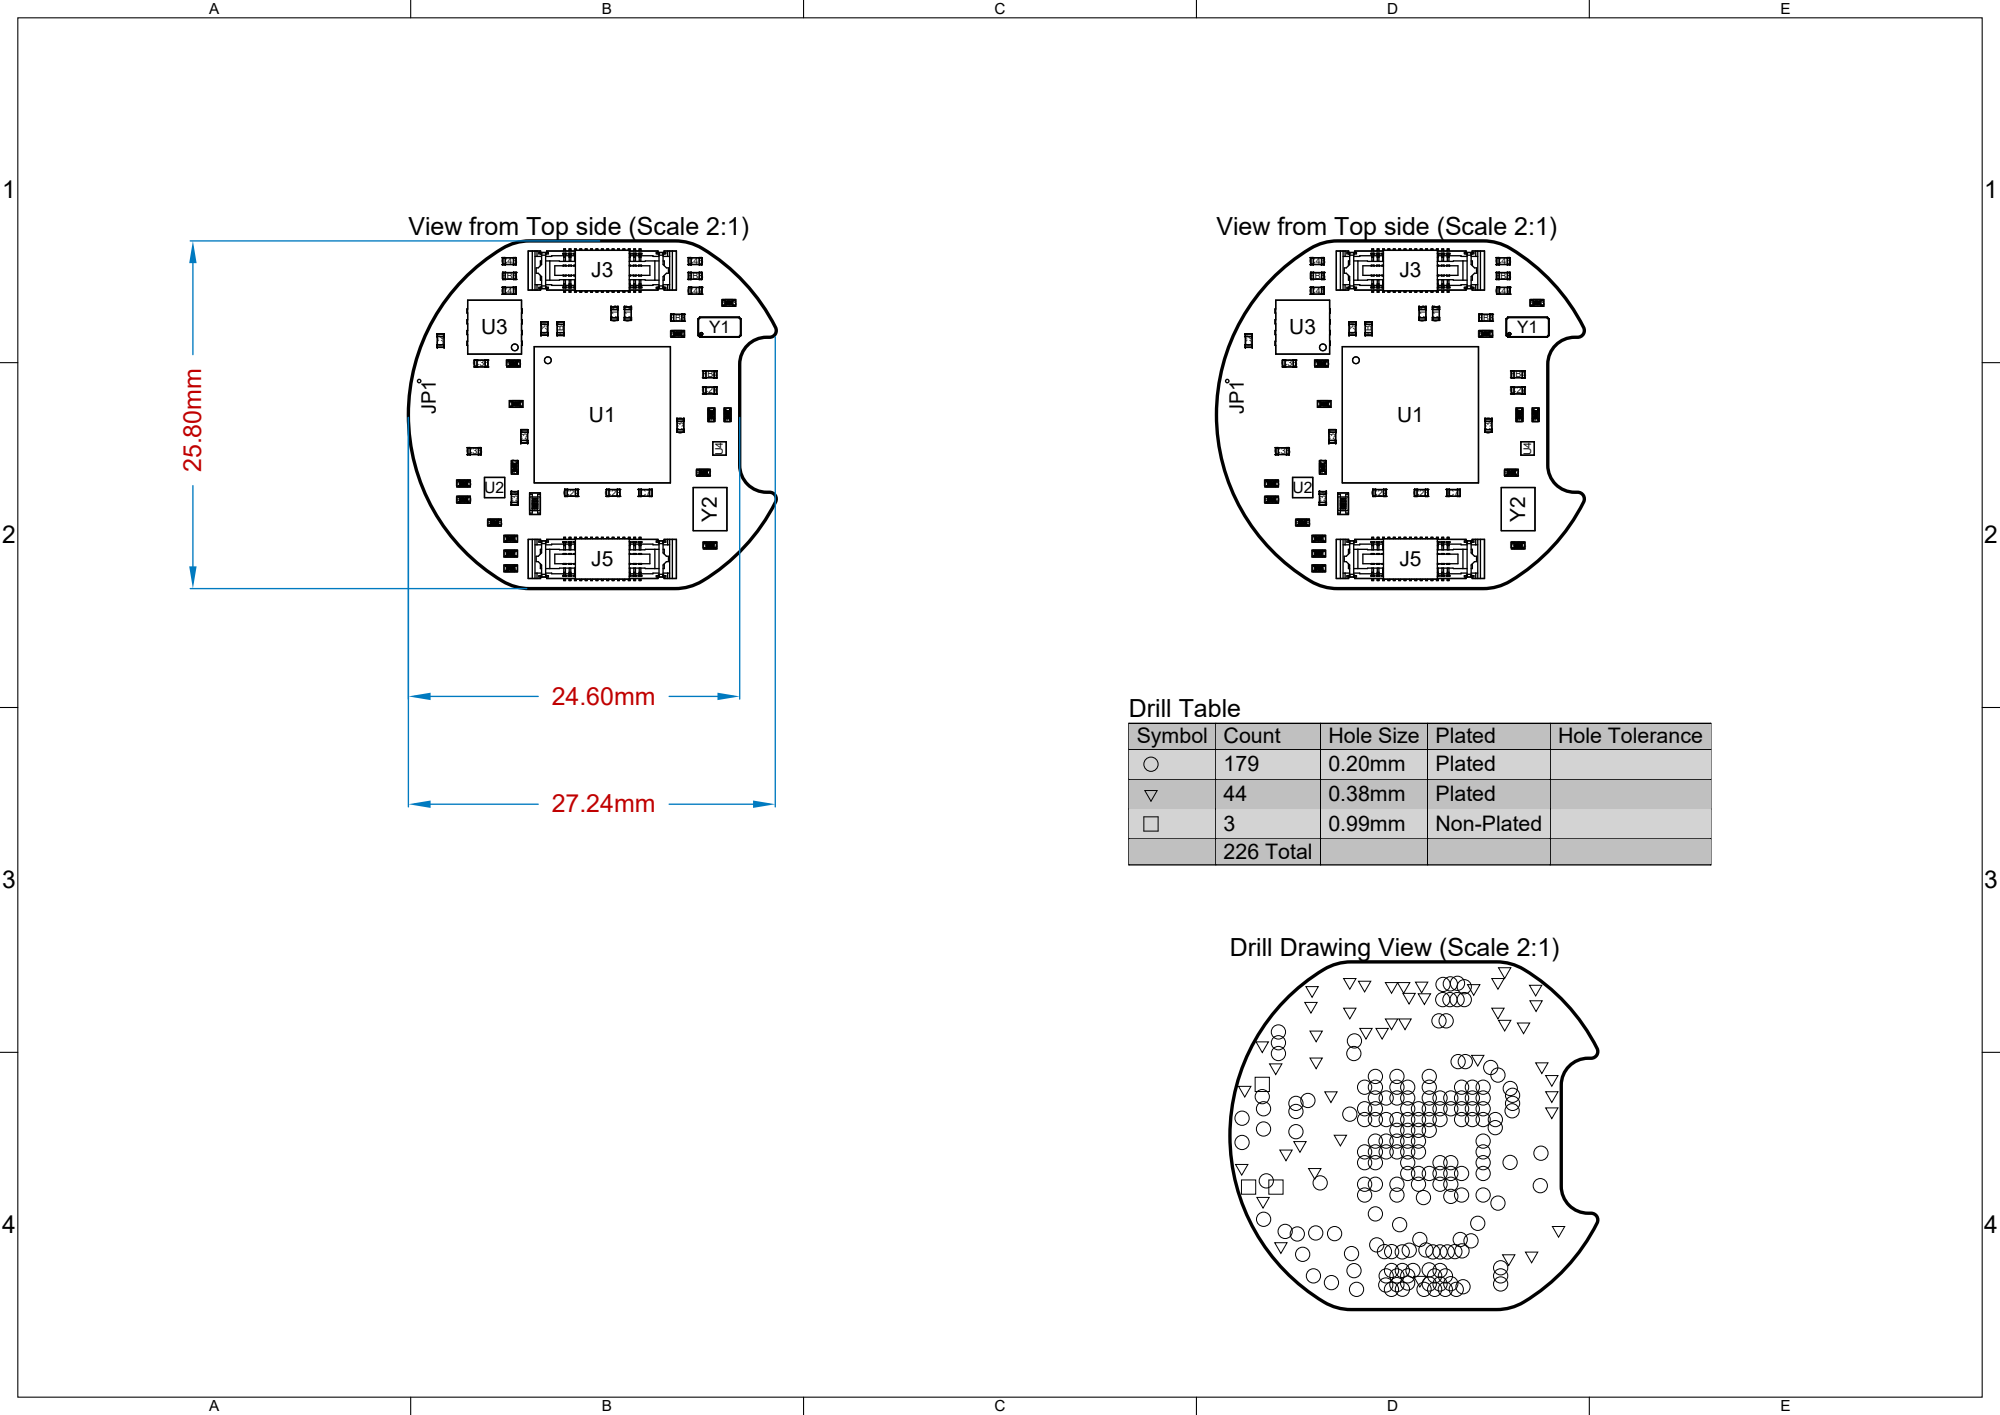
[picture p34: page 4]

View from Top side (Scale 2:1)

Drill Drawing View (Scale 2:1)

# Stack-Up (or similar)

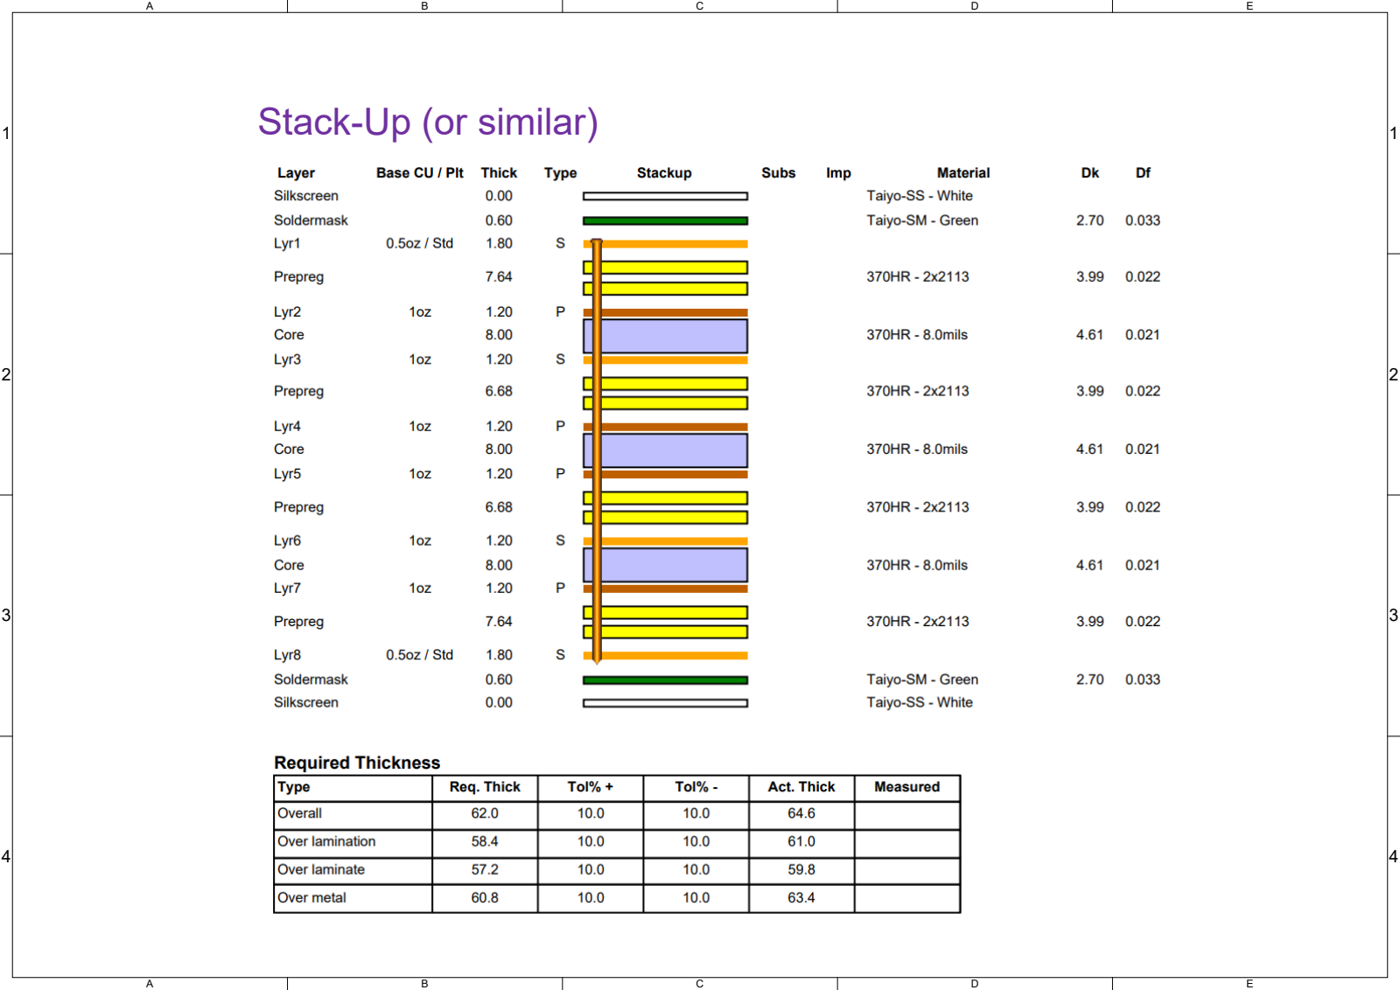
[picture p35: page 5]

1 | 1
2 | 2
3 | 3
4 | 4

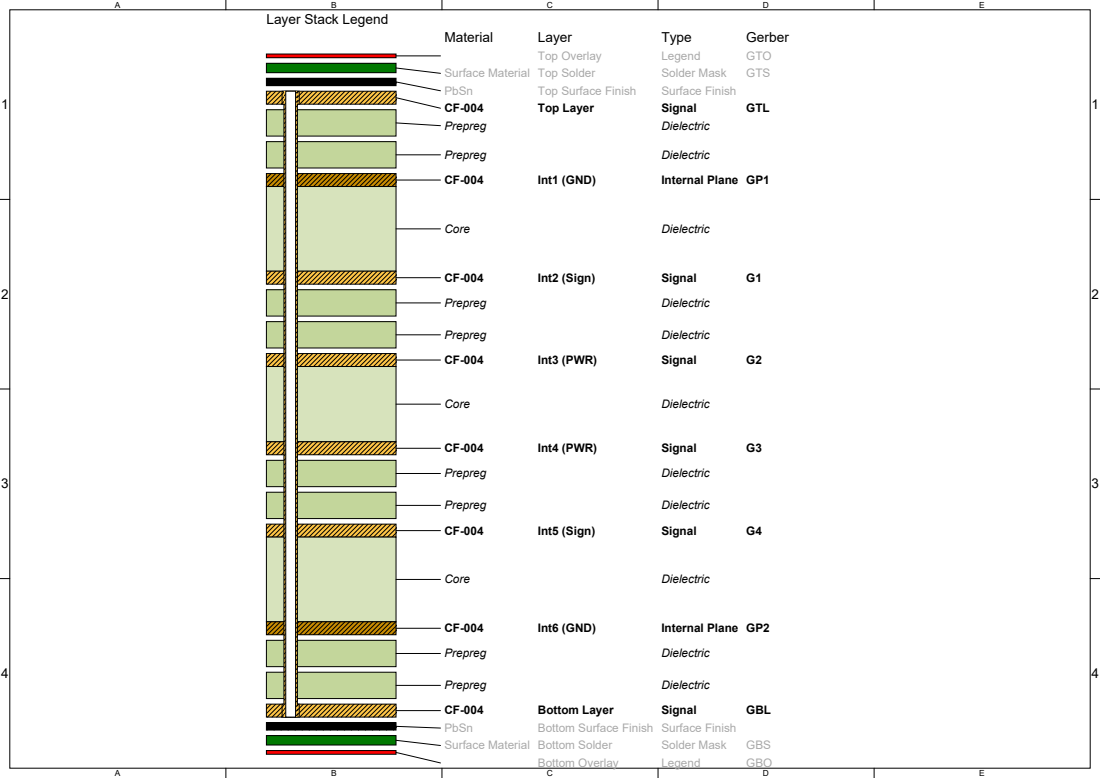
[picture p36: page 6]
Material; Layer; Type; Gerber; Top Overlay; Legend; GTO; Surface Material Top Solder; Solder Mask; GTS; PbSn; Top Surface Finish; Surface Finish; Top Layer; Signal; GTL; Prepreg; Dielectric; Int1 (GND); Internal Plane GP1; Core; Int2 (Sign); Int3 (PWR); Int4 (PWR); Int5 (Sign); Int6 (GND); Internal Plane GP2; Bottom Layer; GBL; Bottom Surface Finish Surface Finish; Surface Material Bottom Solder; GBS; Bottom Overlay; GBO

Layer Stack Legend

1 | 1
2 | 2
3 | 3
4 | 4

Target Impedance
90
100
90
100

Calculated Impedance
90.08
100.91
90.08
100.91

Trace layer
Top Layer
Top Layer
Bottom Layer
Bottom Layer

Wide Trace Width
8.00mil
6.00mil
8.00mil
6.00mil

Narrow Trace Width
8.00mil
6.00mil
8.00mil
6.00mil

Gap
7.00mil
7.00mil
7.00mil
7.00mil

Reference layers
Int1 (GND)
Int1 (GND)
Int6 (GND)
Int6 (GND)

Clearance
5.00mil
5.00mil
5.00mil
5.00mil

Target Tolerance
7%
10%
7%
10%

Transmission Line Structure Table

## Acceptable minimum: 10% target tolerance

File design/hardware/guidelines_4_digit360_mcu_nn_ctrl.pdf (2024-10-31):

A

B

C

D

E

1 | 1

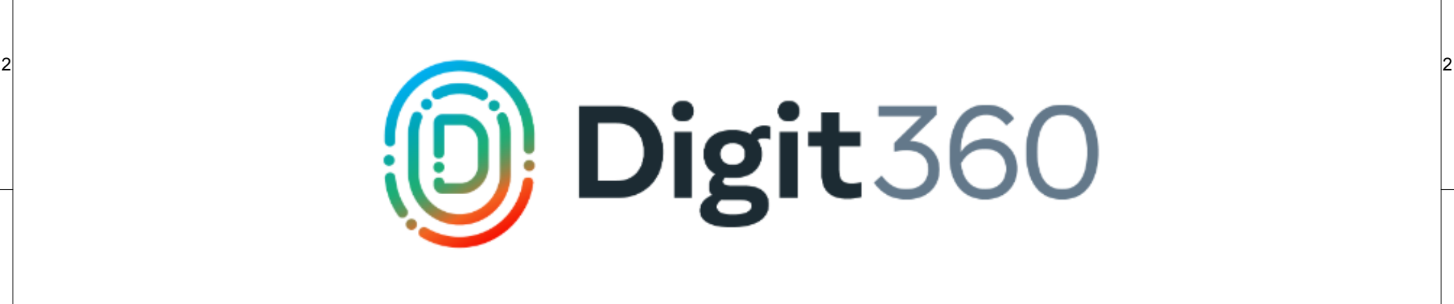
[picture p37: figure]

3 | 3
4 | 4

Copyright (c) Meta Platforms, Inc. and affiliates.
All rights reserved.
This source code is licensed under the license found in the LICENSE file in the root directory of this source tree.

# Digit 360 MCU NN CTRL

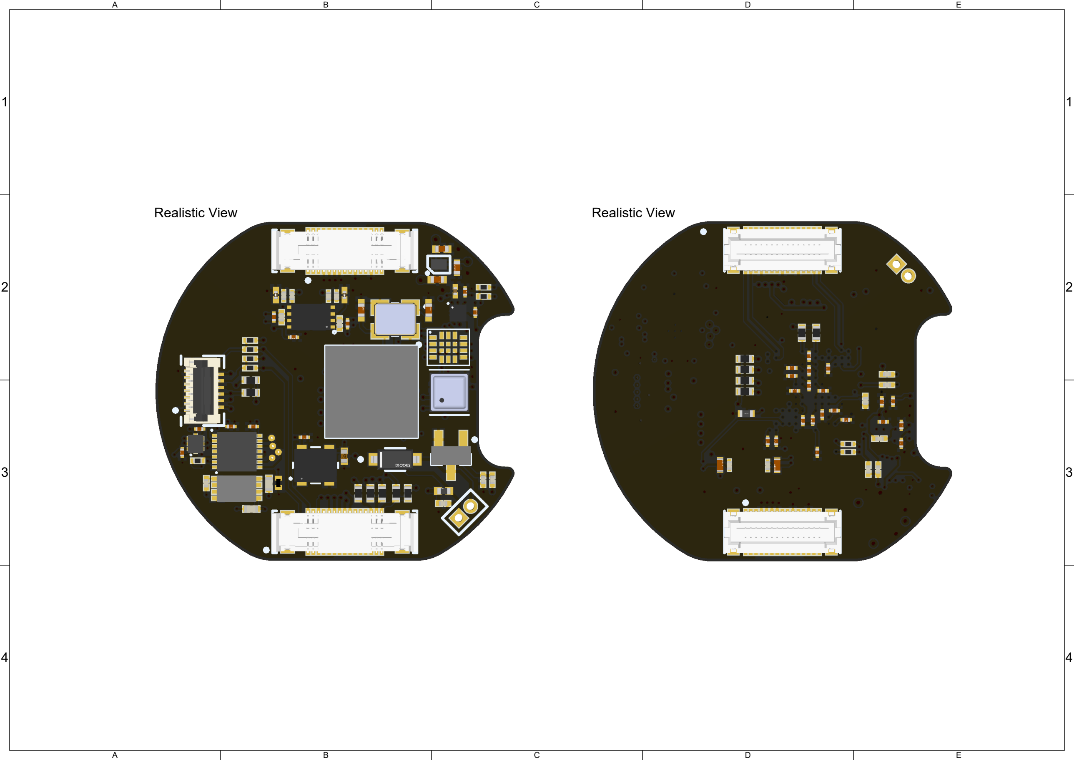
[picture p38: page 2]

1 | 1
2 | 2
3 | 3
4 | 4
Realistic View | Realistic View

1 | 1
2 | 2
3 | 3
4 | 4
1. INTERPRET THIS DRAWING IN ACCORDANCE WITH IPC-D-325A
2. BOARD FABRICATION AND QUALITY PER IPC-6012, CLASS 2, EXCEPT SPECIFIED HEREIN
3. MUST COMPLY WITH EUROPEAN DIRECTIVE 2002/95/EC (RoHS)
4. DIMENSIONAL LIMITS APPLY AFTER PLATING OR COATING
5. BOW AND TWIST MAXIMUM IS 0.75%
MATERIAL: LAMINATE AND PREPREG SHALL BE IN ACCORDANCE WITH IPC-4101/21. 170 DEGREES CELSIUS MINIMUM Tg, UL 94V-0

6.

STACKUP SUMMARY:
A. NUMBER OF COPPER LAYERS: 8
B. BOARD THICKNESS SHALL BE 62mil +/- 10%
C. COPPER: See Layer Stack
D. DEFAULT TRACE/SPACE: 5mil / 5mil
E. CONDUCTOR WIDTH TOLERANCE = +/- 0.01mm

7.

SURFACE FINISH/PLATING:
A. BOARD SHALL BE IMMERSION GOLD PLATED (ENIG) ACCORDING TO IPC-4552. THICKNESS SHALL BE A MINIMUM OF 0.05μm GOLD OVER 3-6μm NICKEL

8.

SOLDERMASK WITH LIQUID PHOTO IMAGEABLE (LPI) PER IPC-SM-840C, CLASS T. COLOR: MATTE BLACK

9.

SILKSCREEN PER SUPPLIED ARTWORK WITH ORGANIC, NON-CONDUCTIVE, EPOXY INK. SILKSCREEN MAY BE TRIMMED OFF ANY SOLDERABLE ENTITY.
COLOR: WHITE

10.

100% BARE BOARD ELECTRICAL TEST TO BE DONE WITH REFERENCE TO SUPPLIED NETLIST

11.

LOCATE MANUFACTURER'S IDENTIFICATION AND LOT CODE ON PRIMARY SIDE FREE FROM ALL METAL ENTITY RENDERED IN SILKSCREEN.

12.

DETAILS NOT SPECIFIED ARE AT MANUFACTURER'S OPTION BUT FINAL APPROVAL MUST BE OBTAINED

13.

NOTES: UNITS IN MILLIMETERS UNLESS OTHERWISE SPECIFIED

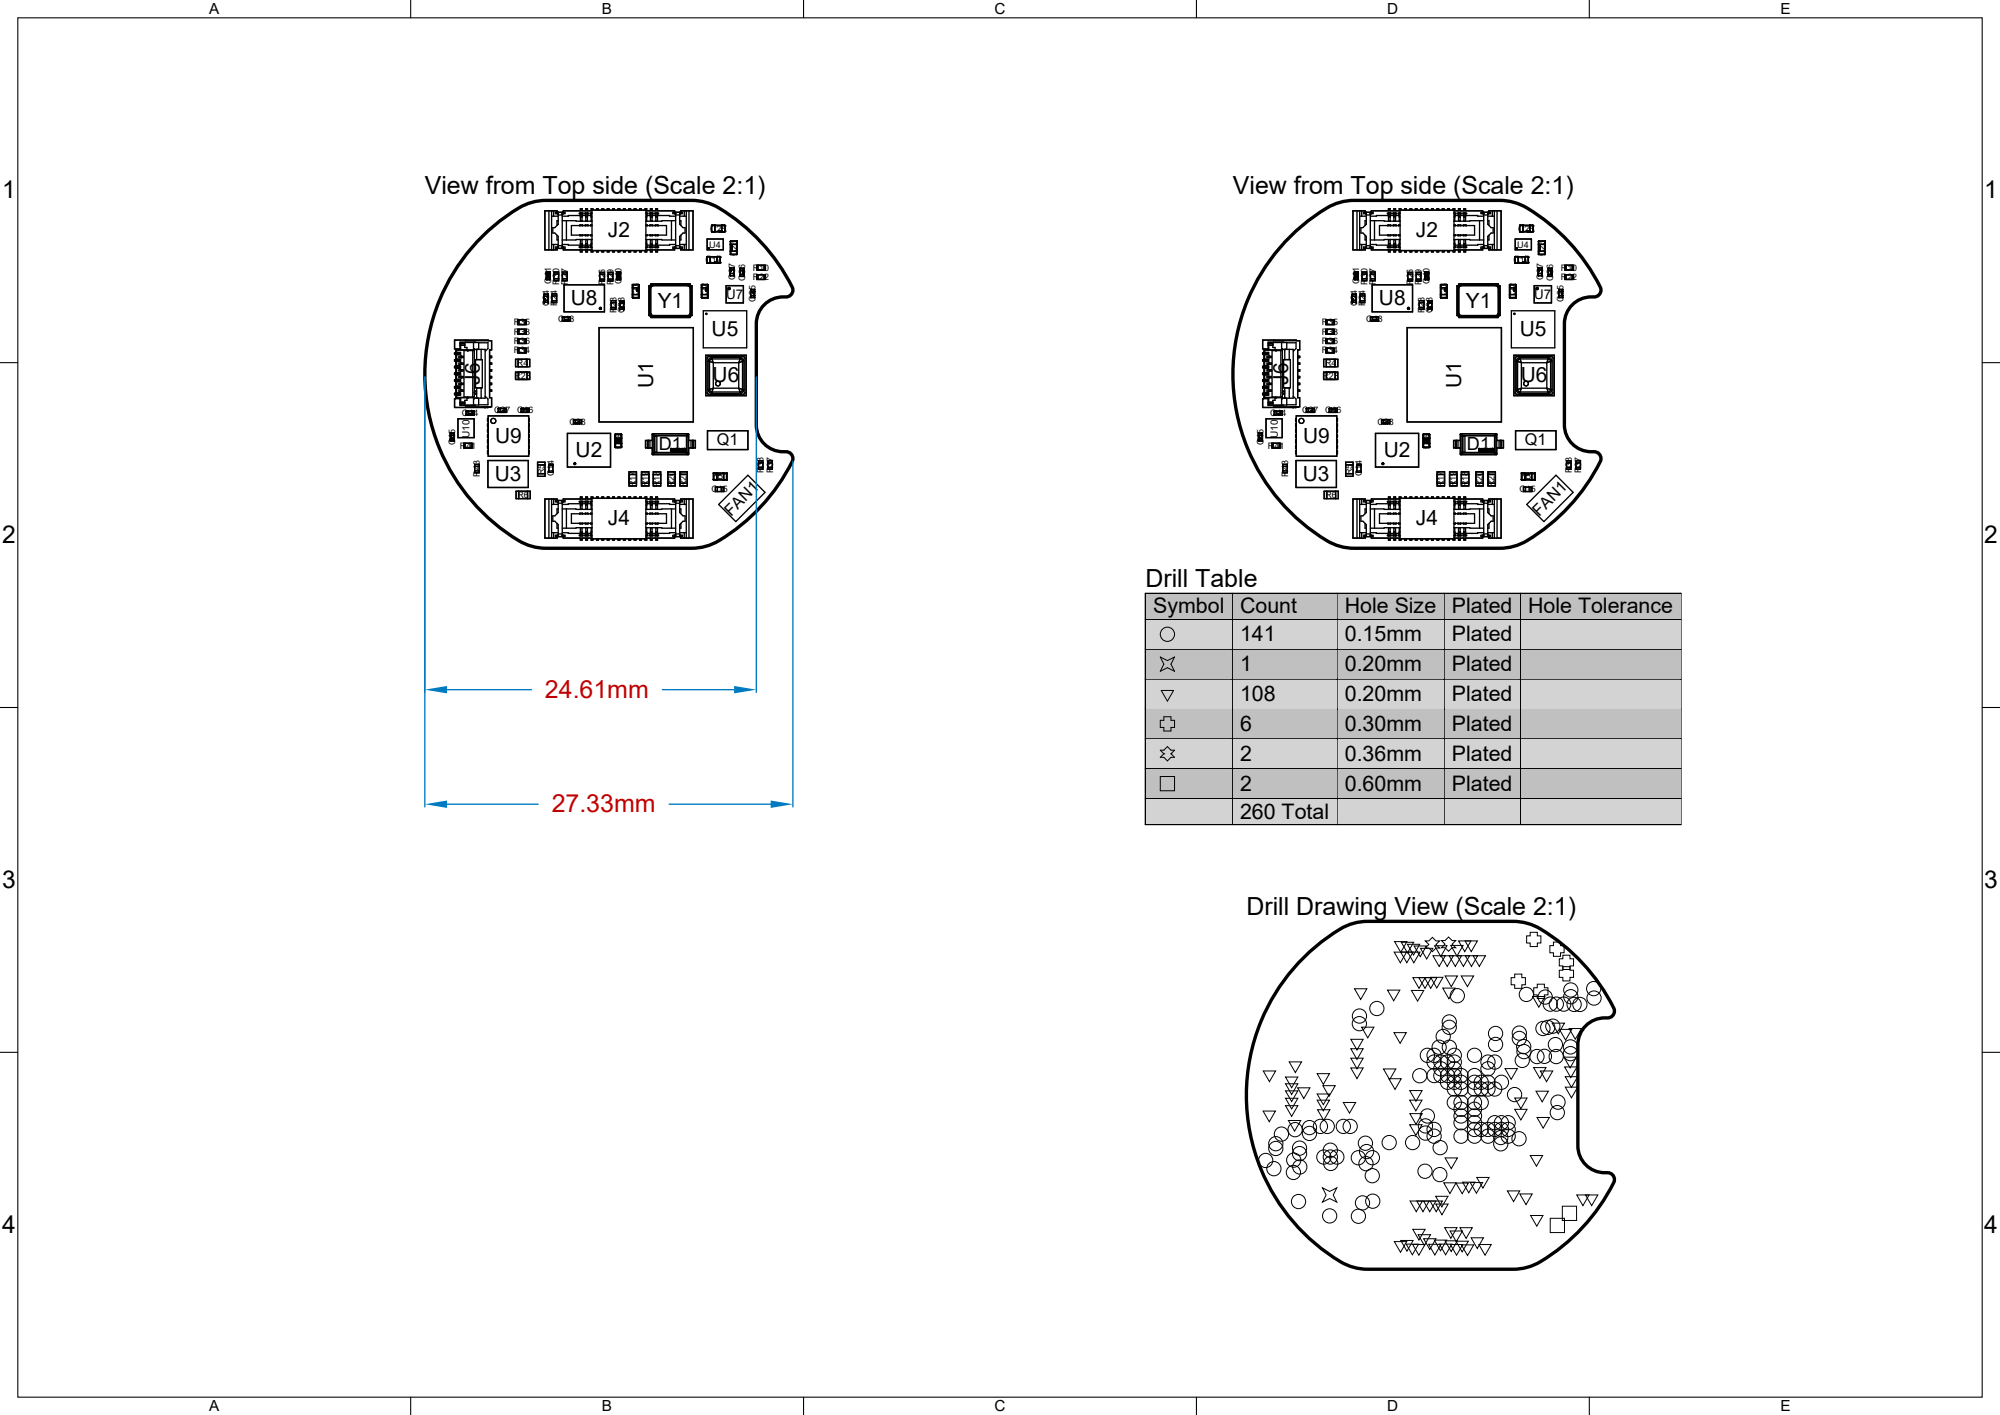
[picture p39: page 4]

View from Top side (Scale 2:1)

Drill Drawing View (Scale 2:1)

# Stack-Up (or similar)

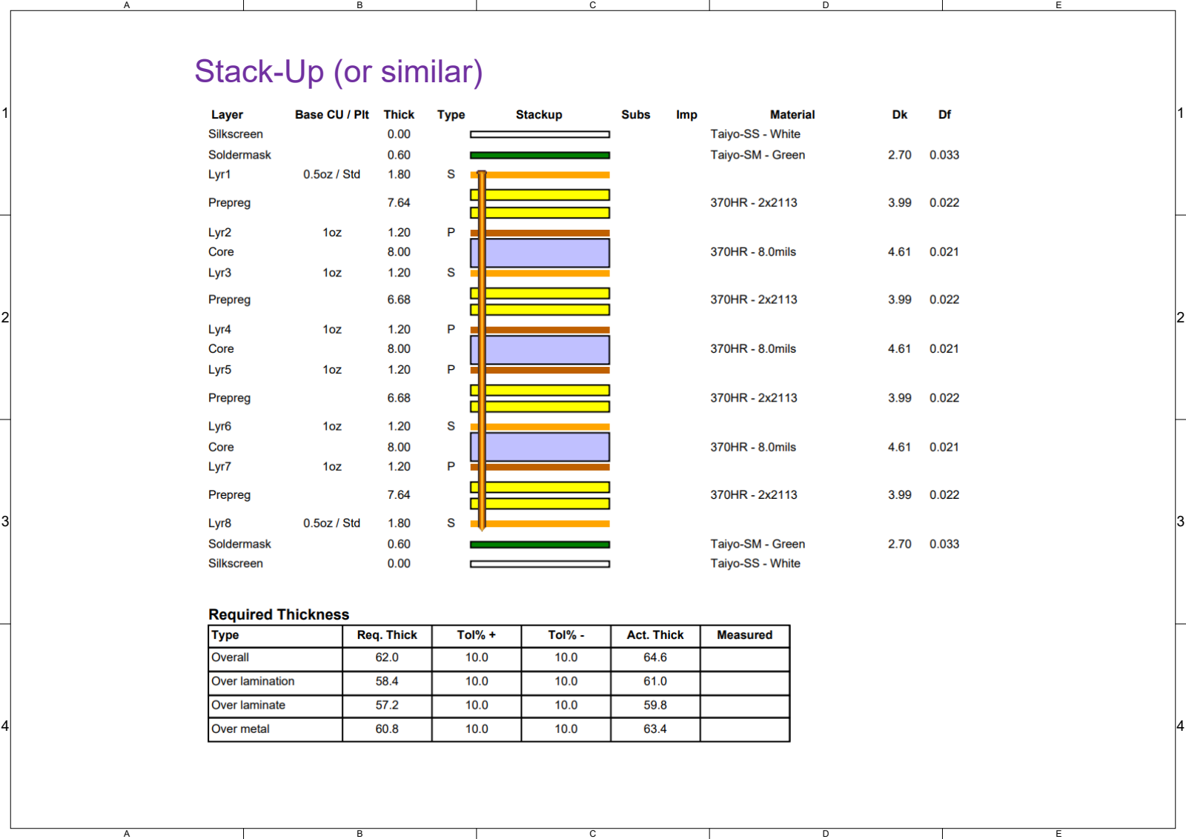
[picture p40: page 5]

1 | 1
2 | 2
3 | 3
4 | 4

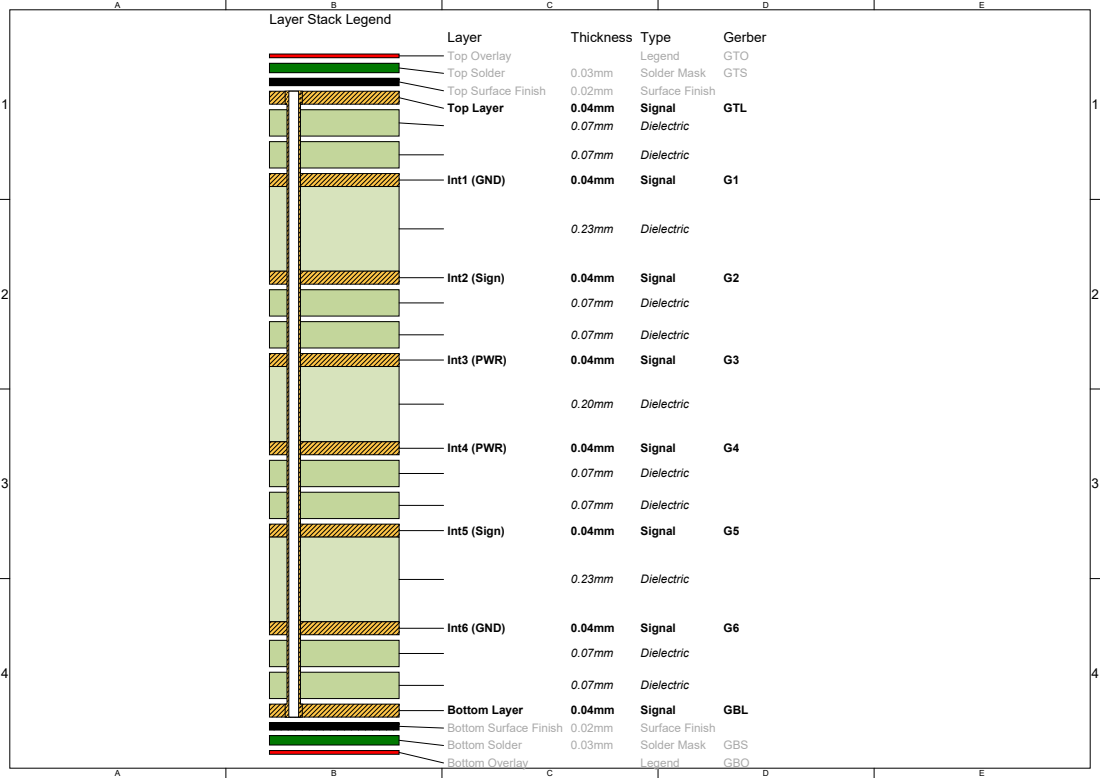
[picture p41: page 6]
Layer; Thickness Type; Gerber; Top Overlay; Legend; GTO; Top Solder; Solder Mask; GTS; Top Surface Finish; Surface Finish; Top Layer; Signal; GTL; Dielectric; Int1 (GND); Int2 (Sign); Int3 (PWR); Int4 (PWR); Int5 (Sign); Int6 (GND); Bottom Layer; GBL; Bottom Surface Finish 0.02mm; Bottom Solder; GBS; Bottom Overlay; GBO

Layer Stack Legend

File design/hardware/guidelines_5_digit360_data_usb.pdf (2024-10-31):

A

B

C

D

E

1 | 1


3 | 3
4 | 4

# Digit 360 Data USB

Copyright (c) Meta Platforms, Inc. and affiliates.
All rights reserved.
This source code is licensed under the license found in the LICENSE file in the root directory of this source tree.

1 | 1

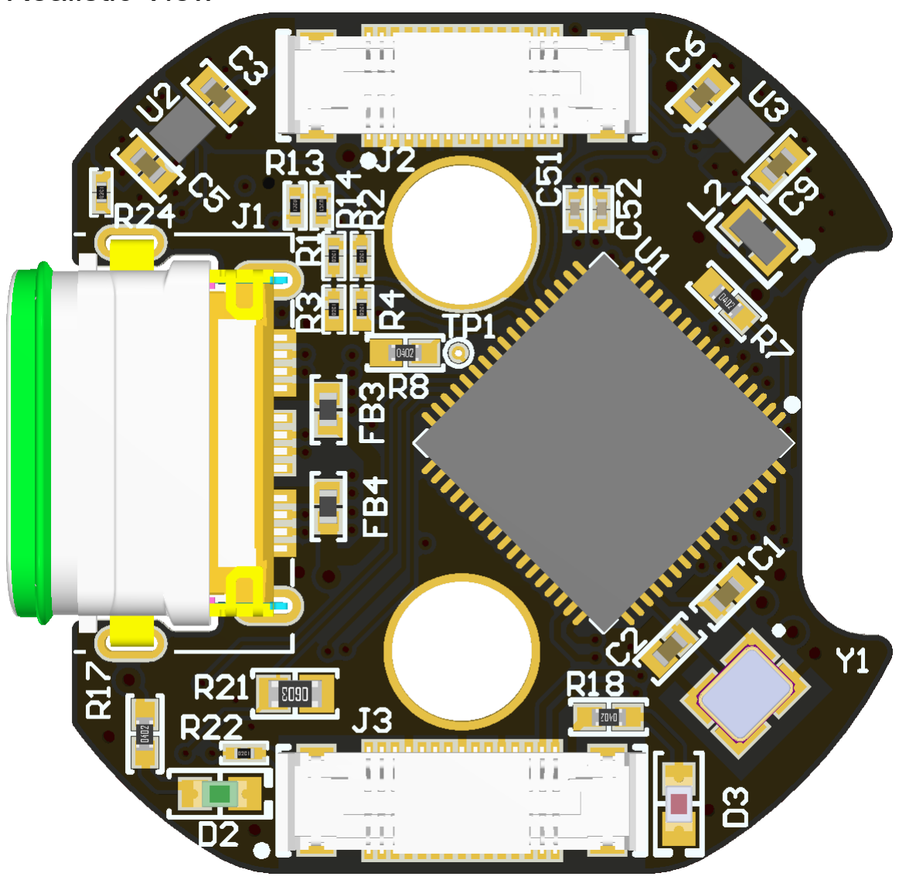
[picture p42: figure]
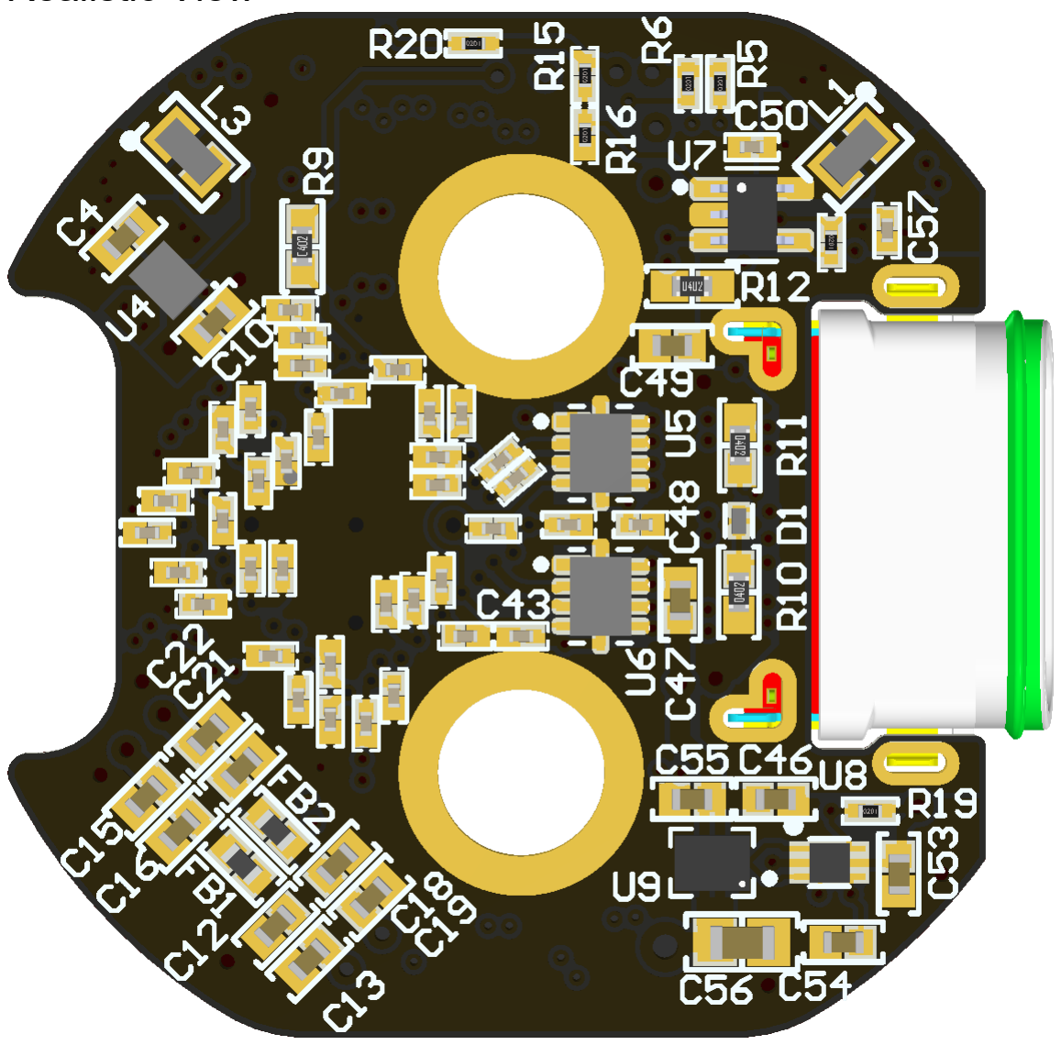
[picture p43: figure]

2 | 2
3 | 3
4 | 4

Realistic View

Realistic View

1 | 1
2 | 2
3 | 3
4 | 4
1. INTERPRET THIS DRAWING IN ACCORDANCE WITH IPC-D-325A
2. BOARD FABRICATION AND QUALITY PER IPC-6012, CLASS 2, EXCEPT SPECIFIED HEREIN
3. MUST COMPLY WITH EUROPEAN DIRECTIVE 2002/95/EC (RoHS)
4. DIMENSIONAL LIMITS APPLY AFTER PLATING OR COATING
5. BOW AND TWIST MAXIMUM IS 0.75%
MATERIAL: LAMINATE AND PREPREG SHALL BE IN ACCORDANCE WITH IPC-4101/21. 170 DEGREES CELSIUS MINIMUM Tg, UL 94V-0

6.

STACKUP SUMMARY:
A. NUMBER OF COPPER LAYERS: 8
B. BOARD THICKNESS SHALL BE 62mil +/- 10%
C. COPPER: See Layer Stack
D. DEFAULT TRACE/SPACE: 4mil / 4mil
E. CONDUCTOR WIDTH TOLERANCE = +/- 0.01mm

7.

VIPPO (VIA IN PAD PLATED OVER) PER IPC-6012, CURRENT REVISION, CLASS 2, AS STATED IN NOTE 2.
a. FILL AND CAP All 0.2mm VIA HOLES WITH NON-CONDUCTIVE EPOXY
b. FILL AND CAP VIAS MUST BE PLANARIZED

8.

SURFACE FINISH/PLATING:
A. BOARD SHALL BE IMMERSION GOLD PLATED (ENIG) ACCORDING TO IPC-4552. THICKNESS SHALL BE A MINIMUM OF 0.05μm GOLD OVER 3-6μm NICKEL

9.

SOLDERMASK WITH LIQUID PHOTO IMAGEABLE (LPI) PER IPC-SM-840C, CLASS T. COLOR: MATTE BLACK

10.

SILKSCREEN PER SUPPLIED ARTWORK WITH ORGANIC, NON-CONDUCTIVE, EPOXY INK. SILKSCREEN MAY BE TRIMMED OFF ANY SOLDERABLE ENTITY.
COLOR: WHITE

11.

100% BARE BOARD ELECTRICAL TEST TO BE DONE WITH REFERENCE TO SUPPLIED NETLIST

12.

LOCATE MANUFACTURER'S IDENTIFICATION AND LOT CODE ON PRIMARY SIDE FREE FROM ALL METAL ENTITY RENDERED IN SILKSCREEN.

13.

DIFFERENTIAL CONTROLLED IMPEDANCE REQUIRED ON BOARD.
SEE TABLE : DIFFERENTIAL CONTROLLED IMPEDANCE
SEE TABLE : SINGLE ENDED CONTROLLED IMPEDANCE

14.

DETAILS NOT SPECIFIED ARE AT MANUFACTURER'S OPTION BUT FINAL APPROVAL MUST BE OBTAINED

15.

NOTES: UNITS IN MILLIMETERS UNLESS OTHERWISE SPECIFIED

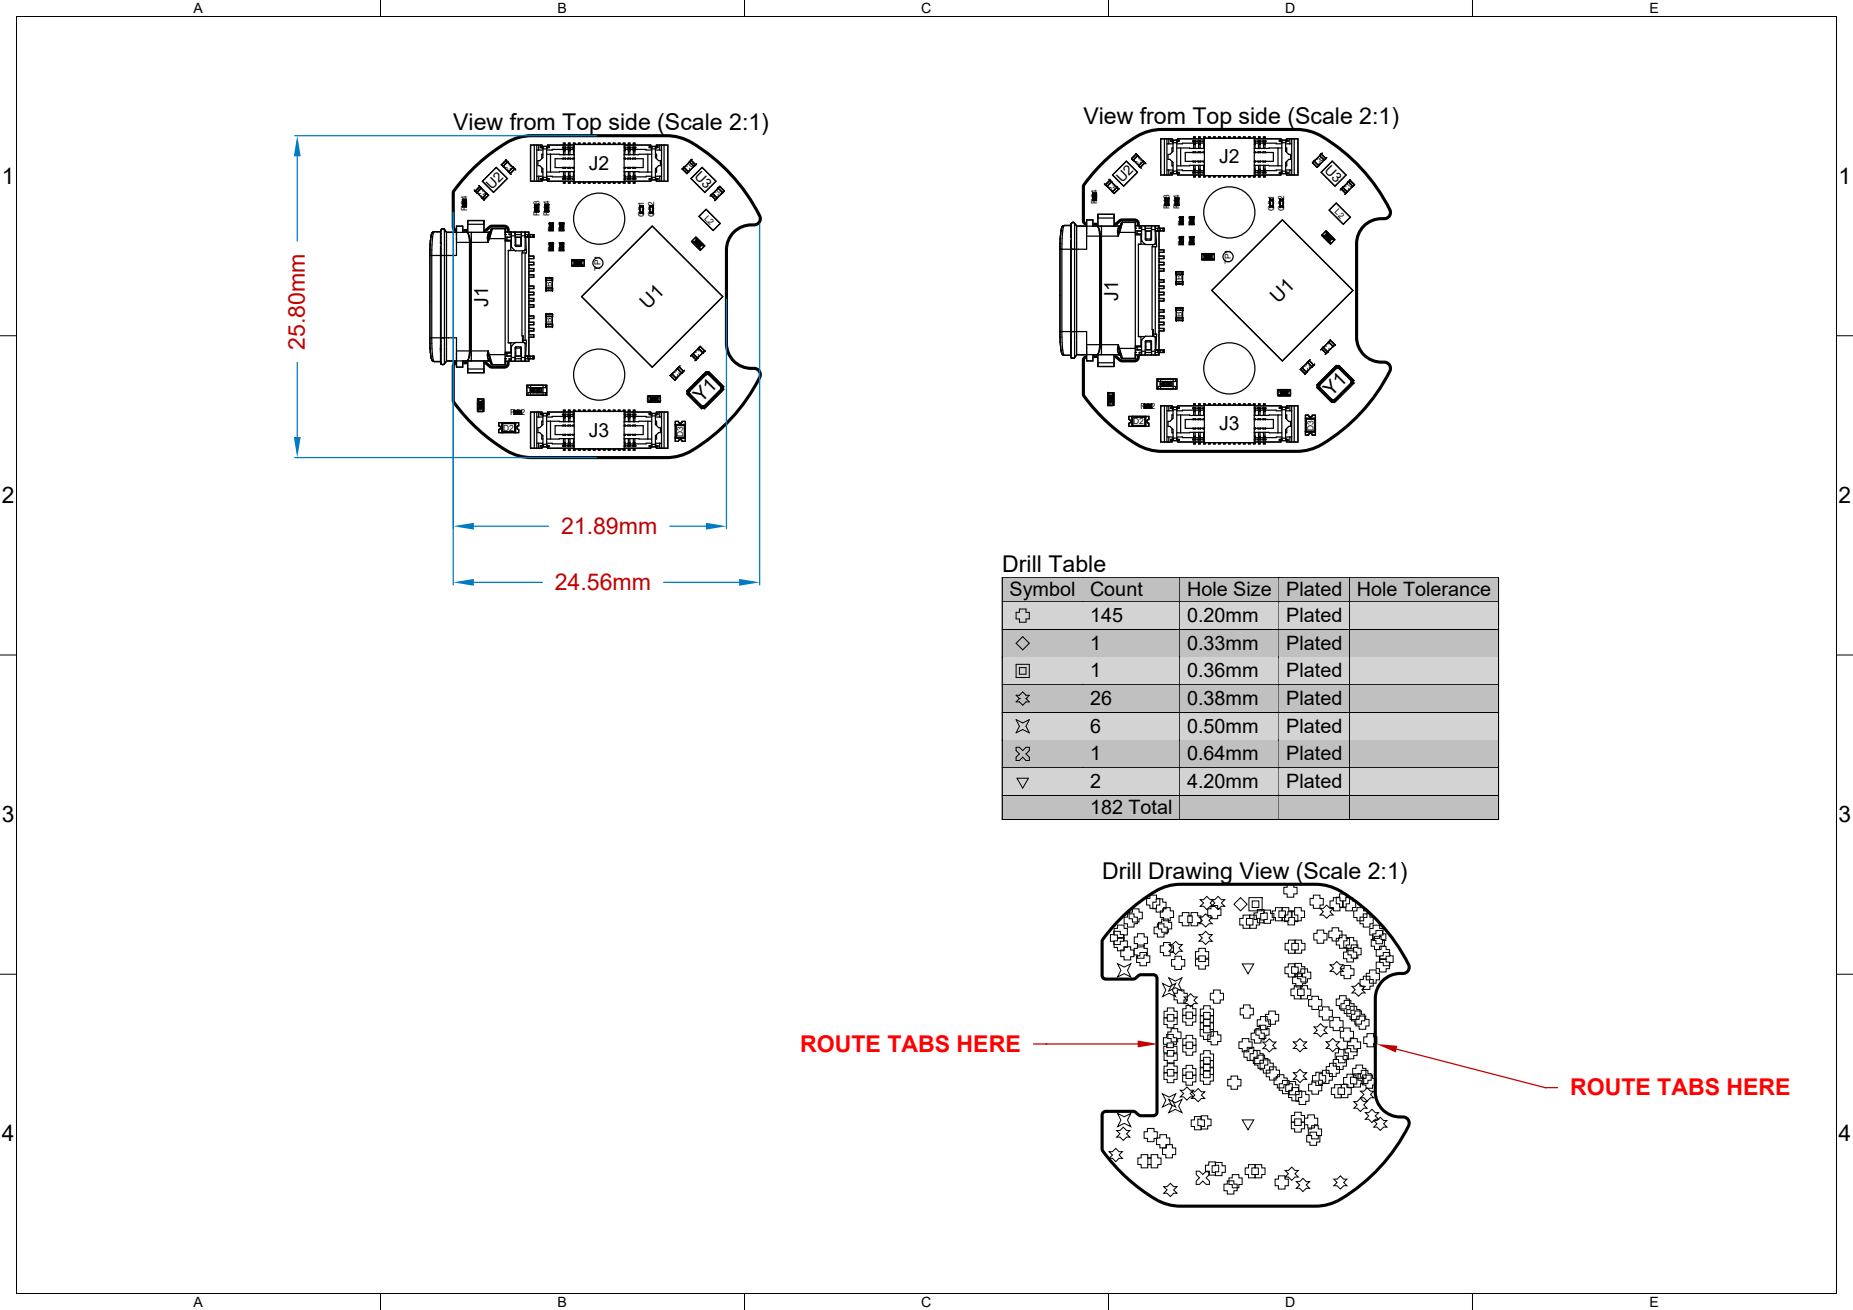
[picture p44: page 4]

View from Top side (Scale 2:1)

Drill Drawing View (Scale 2:1)

# Stack-Up (or similar)

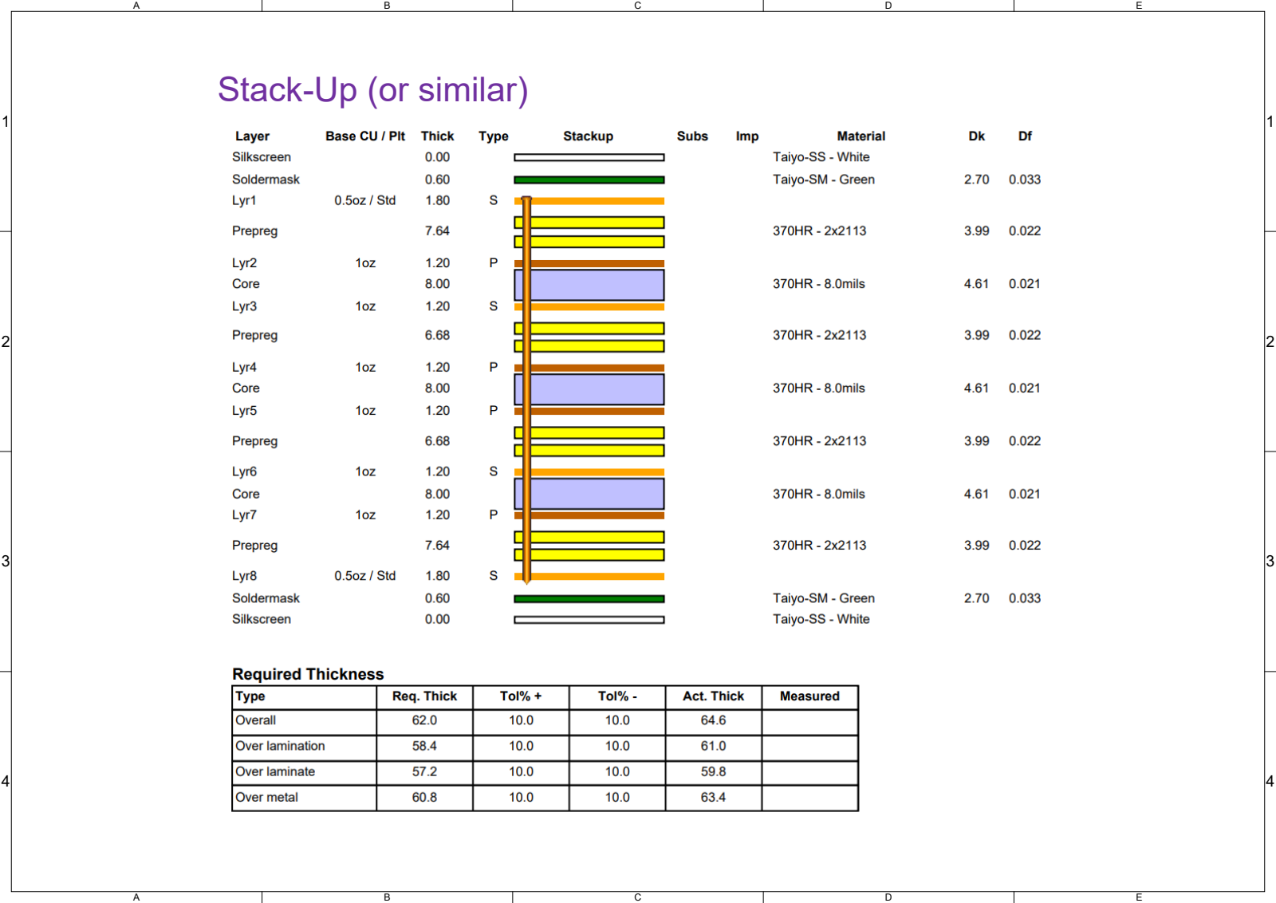
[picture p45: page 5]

1 | 1
2 | 2
3 | 3
4 | 4

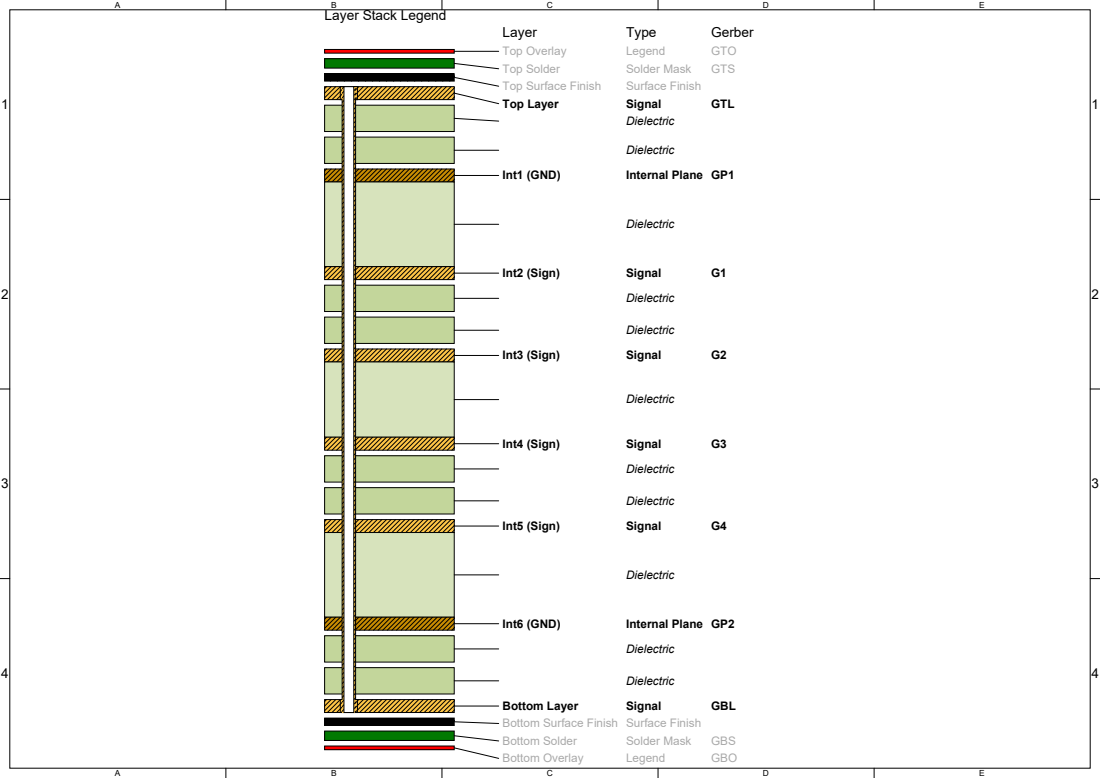
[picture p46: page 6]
Layer; Type; Gerber; Top Overlay; Legend; GTO; Top Solder; Solder Mask; GTS; Top Surface Finish; Surface Finish; Top Layer; Signal; GTL; Dielectric; Int1 (GND); Internal Plane GP1; Int2 (Sign); Int3 (Sign); Int4 (Sign); Int5 (Sign); Int6 (GND); Internal Plane GP2; Bottom Layer; GBL; Bottom Solder; GBS; Bottom Overlay; GBO

Layer Stack Legend

Bottom Surface Finish Surface Finish

1 | 1
2 | 2
3 | 3
4 | 4

Target Impedance
90
90
90
90
90
90

Calculated Impedance
90.08
89.52
88.34
88.34
89.52
90.08

Trace layer
Top Layer
Int2 (Sign)
Int3 (Sign)
Int4 (Sign)
Int5 (Sign)
Bottom Layer

Wide Trace Width
8.00mil
5.00mil
5.00mil
5.00mil
5.00mil
8.00mil

Narrow Trace Width
8.00mil
5.00mil
5.00mil
5.00mil
5.00mil
8.00mil

Gap
7.00mil
8.00mil
8.00mil
8.00mil
8.00mil
7.00mil

Reference layers
Int1 (GND)
Int1 (GND),Int3 (Sign)
Int2 (Sign),Int4 (Sign)
Int3 (Sign),Int5 (Sign)
Int4 (Sign),Int6 (GND)
Int6 (GND)

Clearance
5.00mil
5.00mil
0.00mil
0.00mil
5.00mil
5.00mil

Target Tolerance
7%
7%
7%
7%
7%
7%

Transmission Line Structure Table

## Acceptable minimum: 10% target tolerance

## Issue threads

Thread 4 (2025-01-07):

Unable to generate image outputs

arxrean, 2025-01-07:
I connected Digit360 with my computer via usb-c cable and run `python digit360/interface/examples/test_image.py`. I got the following error:

Found 1 DIGIT360 devices: BB0E96B0D0
[ WARN:0@0.078] global cap.cpp:164 open VIDEOIO(CV_IMAGES): raised OpenCV exception:
OpenCV(4.10.0) /io/opencv/modules/videoio/src/cap_images.cpp:300: error: (-215:Assertion failed) !_filename.empty() in function 'open'
Traceback (most recent call last):
  File "/home/zkou/Code/digit360/digit360/interface/examples/test_image.py", line 20, in <module>
    cv2.imshow('Digit 360', frame)
cv2.error: OpenCV(4.10.0) /io/opencv/modules/highgui/src/window.cpp:973: error: (-215:Assertion failed) size.width>0 && size.height>0 in function 'imshow'.
'
There seems no image output from the Digit360 sensor.

Here is the output from `python digit360/interface/examples/test_usb.py`.

Found 1 DIGIT360 devices: BB0E96B0D0

[Digit360Descriptor(serial='BB0E96B0D0', data='/dev/ttyACM0', audio='hw:3,0', ics='', base_version='0122', ics_version='')]

chaitanyantr, 2025-01-07:
Hi @arxrean

[Digit360Descriptor(serial='BB0E96B0D0', data='/dev/ttyACM0', audio='hw:3,0', ics='', base_version='0122', ics_version='')]
The Digit360Descriptor is not filled with ics and ics_version. **ics='',ics_version=''.**

A filled Digit360Descriptor looks like as follows with right cable.
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

 Please make cure the cable used have faster data transfer (USB 3.2 Gen 2) that supports 10Gbps data transfer speeds.

arxrean, 2025-01-07:
Thank you so much for the help! Now I can successfully run `test_image.py` and see the streaming images.

But it seems the generated images are just dark with RGB average value around (0, 1.0, 0). Is this expected? Should I change some settings such as for led?

arxrean, 2025-01-07:
Thanks for your reply. I tried running `test_led.py` but got the error:

Found 1 DIGIT360 devices: BB0E96B0D0

Traceback (most recent call last):
  File "/home/zkou/Code/digit360/digit360/interface/examples/test_led.py", line 19, in <module>
    led_all_off(descriptor)
  File "/home/zkou/Code/digit360/digit360/interface/control/led.py", line 19, in led_all_off
    if dev.is_open:
       ^^^^^^^^^^^
AttributeError: 'Digit360Descriptor' object has no attribute 'is_open'

arxrean, 2025-01-07:
The issue was gone after I changed the input to led_all_off to Digit360 and added led_set_channel functions.

Thank you for the help!

Closed 2025-01-07.

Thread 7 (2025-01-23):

What is the optimal intensity for rgb in led?

Jonnyboyyyy, 2025-01-23:
I ran test_led.py then test_image.py. It seems like the light intensity is too high.
In test_led.py, it is set to 255 for rgb channels.

led_all_off(Digit360(descriptor.data))
led_set_channel(Digit360(descriptor.data), d360frame.LightingChannel.CHANNEL_1, (255, 0, 0))
led_set_channel(Digit360(descriptor.data), d360frame.LightingChannel.CHANNEL_2, (0, 255, 0))
led_set_channel(Digit360(descriptor.data), d360frame.LightingChannel.CHANNEL_3, (0, 0, 255))

255 seems too bright to capture any useful data. What is the intensity used in Digit360 paper?

Below is the image obtained by setting 255 for RGB.

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

AlphaBetaPhi, 2025-03-25:
Hi @Jonnyboyyyy , I would recommend starting from each individual channel at 10-13 and then increasing. We allow for a large range for different experimentations with the artificial fingertip gel material.

Closed 2025-03-25.

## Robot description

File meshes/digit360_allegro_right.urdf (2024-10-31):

<?xml version="1.0" encoding="utf-8"?>
<robot name="meta_allegro" xmlns:xacro="http://ros.org/wiki/xacro">
  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
    <link name="allegro_root0">
      <inertial>
        <origin rpy="0 0 0" xyz="0 0 0"/>
        <mass value="4.00000"/>
        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
      </inertial>
    </link>
    <link name="allegro_root1">
      <inertial>
        <mass value="1.05"/>
        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
      </inertial>
    </link>
    <link name="allegro_root2">
      <inertial>
        <mass value="1.05"/>
        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
      </inertial>
    </link>
    <link name="allegro_root3">
      <inertial>
        <mass value="1.05"/>
        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
      </inertial>
    </link>
    <link name="allegro_root4">
      <inertial>
        <mass value="1.05"/>
        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
      </inertial>
    </link>
    <link name="allegro_root5">
      <inertial>
        <mass value="1.05"/>
        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
      </inertial>
    </link>

    <joint name="x_joint" type="prismatic">
      <parent link="allegro_root0"/>
      <child link="allegro_root1"/>
      <axis xyz="1 0 0"/>
      <limit lower="-0.2" upper="0.2"/>
    </joint>
    <joint name="y_joint" type="prismatic">
      <parent link="allegro_root1"/>
      <child link="allegro_root2"/>
      <axis xyz="0 1 0"/>
      <limit lower="-0.2" upper="0.2"/>
    </joint>
    <joint name="z_joint" type="prismatic">
      <parent link="allegro_root2"/>
      <child link="allegro_root3"/>
      <axis xyz="0 0 1"/>
      <limit lower="-0.2" upper="0.2"/>
    </joint>
    <joint name="x_rotation_joint" type="revolute">
      <parent link="allegro_root3"/>
      <child link="allegro_root4"/>
      <axis xyz="1 0 0"/>
        <origin rpy="-0.00000 -0.00000 0" xyz="0 0 0.03"/>
      <limit lower="-3.14" upper="3.14"/>
    </joint>
    <joint name="y_rotation_joint" type="revolute">
      <parent link="allegro_root4"/>
      <child link="allegro_root5"/>
      <axis xyz="0 1 0"/>
      <origin rpy="-0.00000 -0.00000 0" xyz="0 0 0.03"/>
      <limit lower="-3.14" upper="3.14"/>
    </joint>
    <joint name="z_rotation_joint" type="revolute">
      <parent link="allegro_root5"/>
      <child link="base_link"/>
      <axis xyz="0 0 1"/>
      <origin rpy="-0.00000 -0.00000 0" xyz="0 0 0.03"/>
      <limit lower="-3.14" upper="3.14"/>
    </joint>

    <link name="base_link">
    <inertial>
      <mass value="0.4154"/>
      <origin rpy="0 0 0" xyz="0 0 0"/>
      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
    </inertial>
    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
    
  </link>


  <link name="link_0.0">
    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
    <inertial>
      <mass value="0.0119"/>
      <origin rpy="0 0 0" xyz="0 0 0"/>
      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
    </inertial>

    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
  </link>
  <joint name="joint_0.0" type="revolute">
    <axis xyz="0 0 1"/>
    <limit effort="0" lower="-0.47" upper="0.47" velocity="10"/>
    <parent link="base_link"/>
    <child link="link_0.0"/>
    <origin rpy="-0.08726646255 0 0" xyz="0 0.0435 -0.001542"/>
  </joint>
  <link name="link_1.0">
    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
     <inertial>
      <mass value="0.065"/>
      <origin rpy="0 0 0" xyz="0 0 0"/>
      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
    </inertial>
    
    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
  </link>
  <joint name="joint_1.0" type="revolute">
    <limit effort="0" lower="-0.196" upper="1.61" velocity="10"/>
    <axis xyz="0 1 0"/>
    <parent link="link_0.0"/>
    <child link="link_1.0"/>
    <origin xyz="0 0 0.0164"/>
  </joint>
  <link name="link_2.0">
    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
    <inertial>
      <mass value="0.0355"/>
      <origin rpy="0 0 0" xyz="0 0 0"/>
      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
    </inertial>

    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
  </link>
  <joint name="joint_2.0" type="revolute">
    <axis xyz="0 1 0"/>
    <limit effort="0" lower="-0.174" upper="1.709" velocity="10"/>
    <parent link="link_1.0"/>
    <child link="link_2.0"/>
    <origin xyz="0 0 0.054"/>
  </joint>
  <link name="link_3.0">
    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
     <inertial>
      <mass value="0.0096"/>
      <origin rpy="0 0 0" xyz="0 0 0"/>
      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
    </inertial>

    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
  </link>
  <joint name="joint_3.0" type="revolute">
    <axis xyz="0 1 0"/>
    <limit effort="0" lower="-0.227" upper="1.618" velocity="10"/>
    <parent link="link_2.0"/>
    <child link="link_3.0"/>
    <origin xyz="0 0 0.0384"/>
  </joint>

  <link name="link_4.0">
    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

    <inertial>
      <mass value="0.0119"/>
      <origin rpy="0 0 0" xyz="0 0 0"/>
      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
    </inertial>

    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
  </link>
  <joint name="joint_4.0" type="revolute">
    <axis xyz="0 0 1"/>
    <limit effort="0" lower="-0.47" upper="0.47" velocity="10"/>
    <parent link="base_link"/>
    <child link="link_4.0"/>
    <origin rpy="0.0 0 0" xyz="0 0 0.0007"/>
  </joint>
  <link name="link_5.0">
    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
    
    <inertial>
      <mass value="0.065"/>
      <origin rpy="0 0 0" xyz="0 0 0"/>
      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
    </inertial>

    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
  </link>
  <joint name="joint_5.0" type="revolute">
    <limit effort="0" lower="-0.196" upper="1.61" velocity="10"/>
    <axis xyz="0 1 0"/>
    <parent link="link_4.0"/>
    <child link="link_5.0"/>
    <origin xyz="0 0 0.0164"/>
  </joint>
  <link name="link_6.0">
    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
    <inertial>
      <mass value="0.0355"/>
      <origin rpy="0 0 0" xyz="0 0 0"/>
      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
    </inertial>

    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
  </link>
  <joint name="joint_6.0" type="revolute">
    <axis xyz="0 1 0"/>
    <limit effort="0" lower="-0.174" upper="1.709" velocity="10"/>
    <parent link="link_5.0"/>
    <child link="link_6.0"/>
    <origin xyz="0 0 0.054"/>
  </joint>
  <link name="link_7.0">
    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
    <inertial>
      <mass value="0.0096"/>
      <origin rpy="0 0 0" xyz="0 0 0"/>
      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
    </inertial>

    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
  </link>
  <joint name="joint_7.0" type="revolute">
    <axis xyz="0 1 0"/>
    <limit effort="0" lower="-0.227" upper="1.618" velocity="10"/>
    <parent link="link_6.0"/>
    <child link="link_7.0"/>
    <origin xyz="0 0 0.0384"/>
  </joint>
 
  <link name="link_8.0">
    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

    <inertial>
      <mass value="0.0119"/>
      <origin rpy="0 0 0" xyz="0 0 0"/>
      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
    </inertial>

    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

  </link>
  <joint name="joint_8.0" type="revolute">
    <axis xyz="0 0 1"/>
    <limit effort="0" lower="-0.47" upper="0.47" velocity="10"/>
    <parent link="base_link"/>
    <child link="link_8.0"/>
    <origin rpy="0.08726646255 0 0" xyz="0 -0.0435 -0.001542"/>
  </joint>
  <link name="link_9.0">
    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
    <inertial>
      <mass value="0.065"/>
      <origin rpy="0 0 0" xyz="0 0 0"/>
      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
    </inertial>

    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
  </link>
  <joint name="joint_9.0" type="revolute">
    <limit effort="0" lower="-0.196" upper="1.61" velocity="10"/>
    <axis xyz="0 1 0"/>
    <parent link="link_8.0"/>
    <child link="link_9.0"/>
    <origin xyz="0 0 0.0164"/>
  </joint>
  <link name="link_10.0">
    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
    <inertial>
      <mass value="0.0355"/>
      <origin rpy="0 0 0" xyz="0 0 0"/>
      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
    </inertial>

    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
  </link>
  <joint name="joint_10.0" type="revolute">
    <axis xyz="0 1 0"/>
    <limit effort="0" lower="-0.174" upper="1.709" velocity="10"/>
    <parent link="link_9.0"/>
    <child link="link_10.0"/>
    <origin xyz="0 0 0.054"/>
  </joint>
  <link name="link_11.0">
    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
     <inertial>
      <mass value="0.0096"/>
      <origin rpy="0 0 0" xyz="0 0 0"/>
      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
    </inertial>

    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
  </link>
  <joint name="joint_11.0" type="revolute">
    <axis xyz="0 1 0"/>
    <limit effort="0" lower="-0.227" upper="1.618" velocity="10"/>
    <parent link="link_10.0"/>
    <child link="link_11.0"/>
    <origin xyz="0 0 0.0384"/>
  </joint>

  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
  <link name="link_12.0">
    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
    <inertial>
      <mass value="0.0176"/>
      <origin rpy="0 0 0" xyz="0 0 0"/>
      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
    </inertial>

    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
  </link>
  <joint name="joint_12.0" type="revolute">
    <axis xyz="-1 0 0"/>
    <limit effort="0" lower="0.263" upper="1.396" velocity="10"/>
    <parent link="base_link"/>
    <child link="link_12.0"/>
    <origin rpy="0 -1.65806278845 -1.5707963259" xyz="-0.0182 0.019333 -0.045987"/>
  </joint>
  <link name="link_13.0">
    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
    <inertial>
      <mass value="0.0119"/>
      <origin rpy="0 0 0" xyz="0 0 0"/>
      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
    </inertial>
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

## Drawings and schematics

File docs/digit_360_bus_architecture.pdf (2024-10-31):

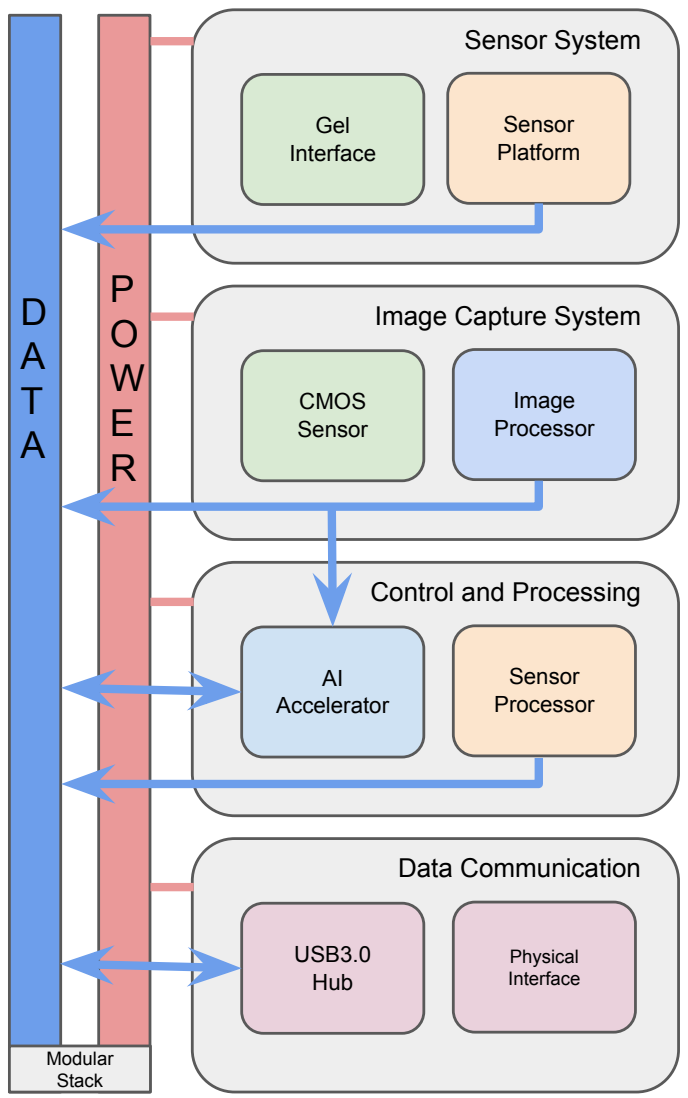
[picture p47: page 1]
CMOS Sensor; Image Processor; AI Accelerator; Sensor Processor; Sensor System; Gel Interface; Sensor Platform; Data Communication; USB3.0 Hub; Physical Interface; Modular Stack

Image Capture System

Control and Processing

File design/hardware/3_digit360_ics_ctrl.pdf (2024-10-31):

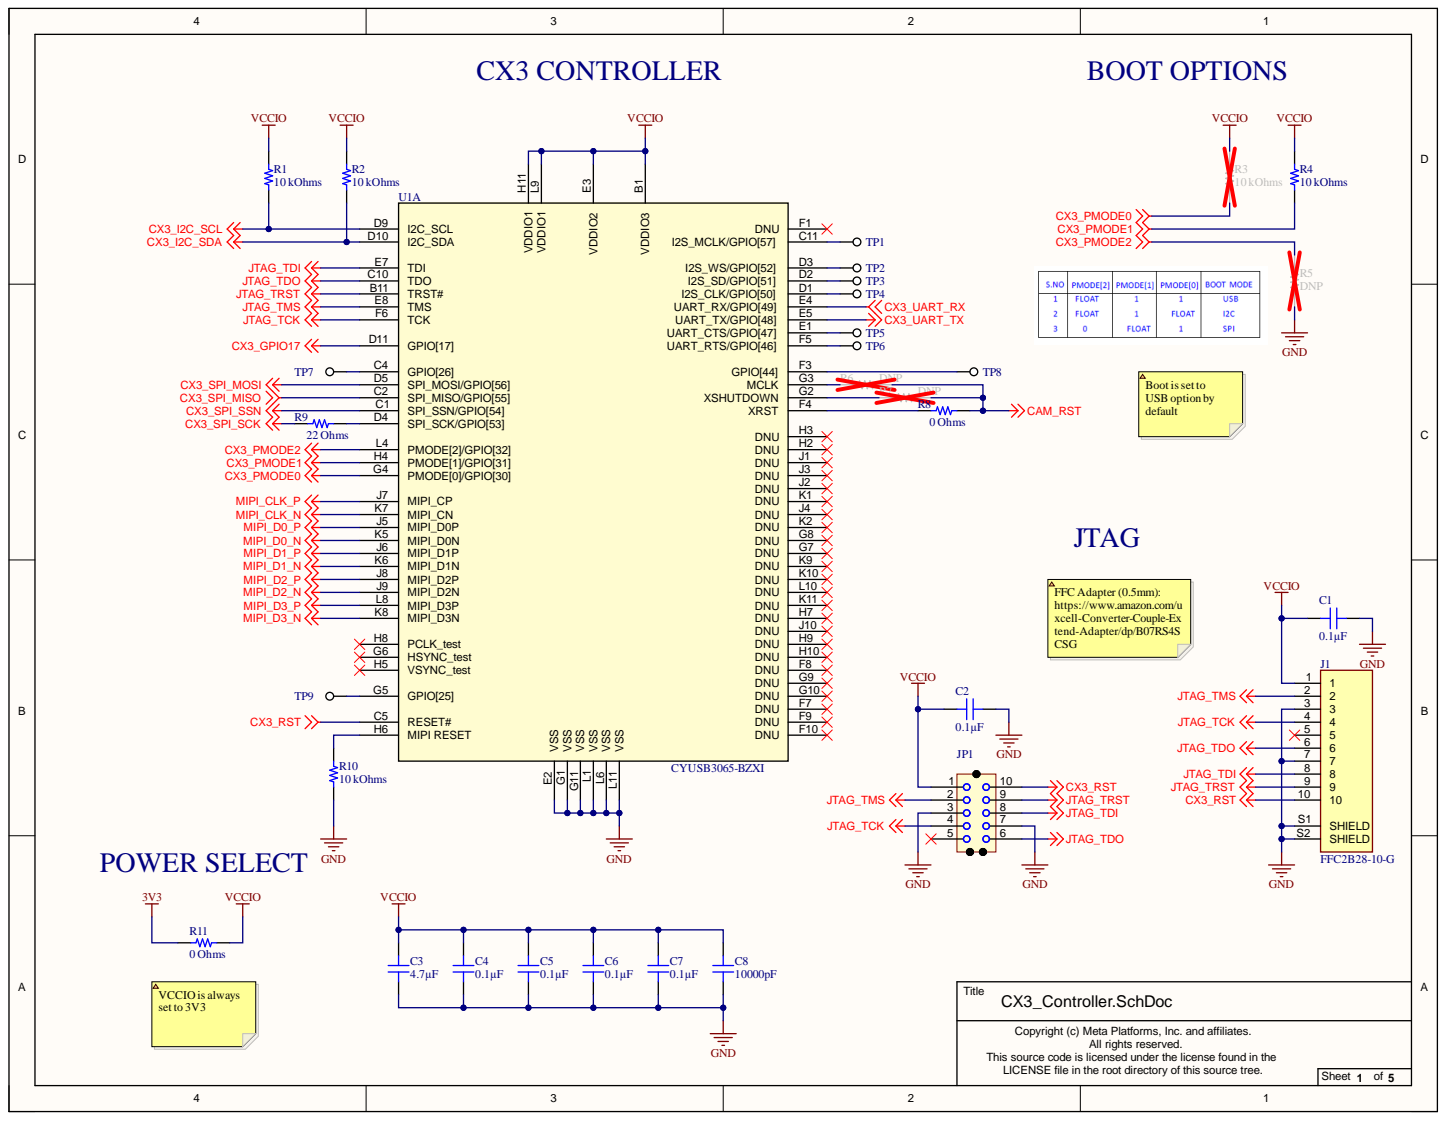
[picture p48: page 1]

FFC Adapter (0.5mm):
https://www.amazon.com/u
xcell-Converter-Couple-Ex
tend-Adapter/dp/B07RS4S
CSG

Copyright (c) Meta Platforms, Inc. and affiliates.

This source code is licensed under the license found in the
LICENSE file in the root directory of this source tree.

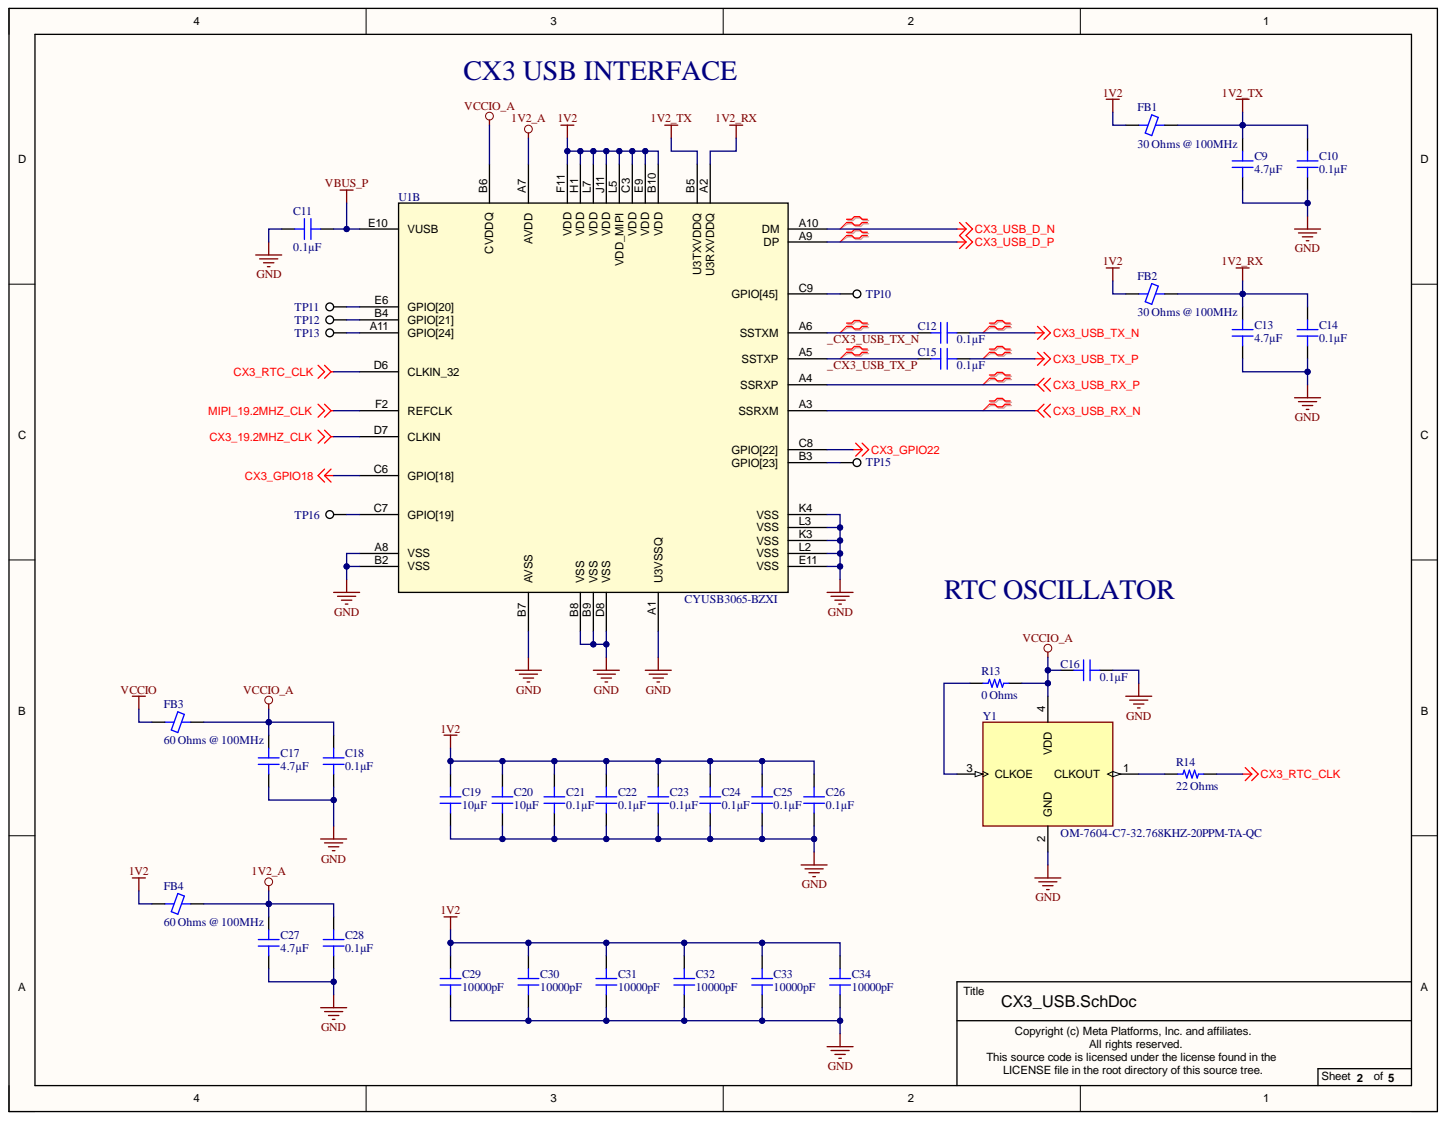
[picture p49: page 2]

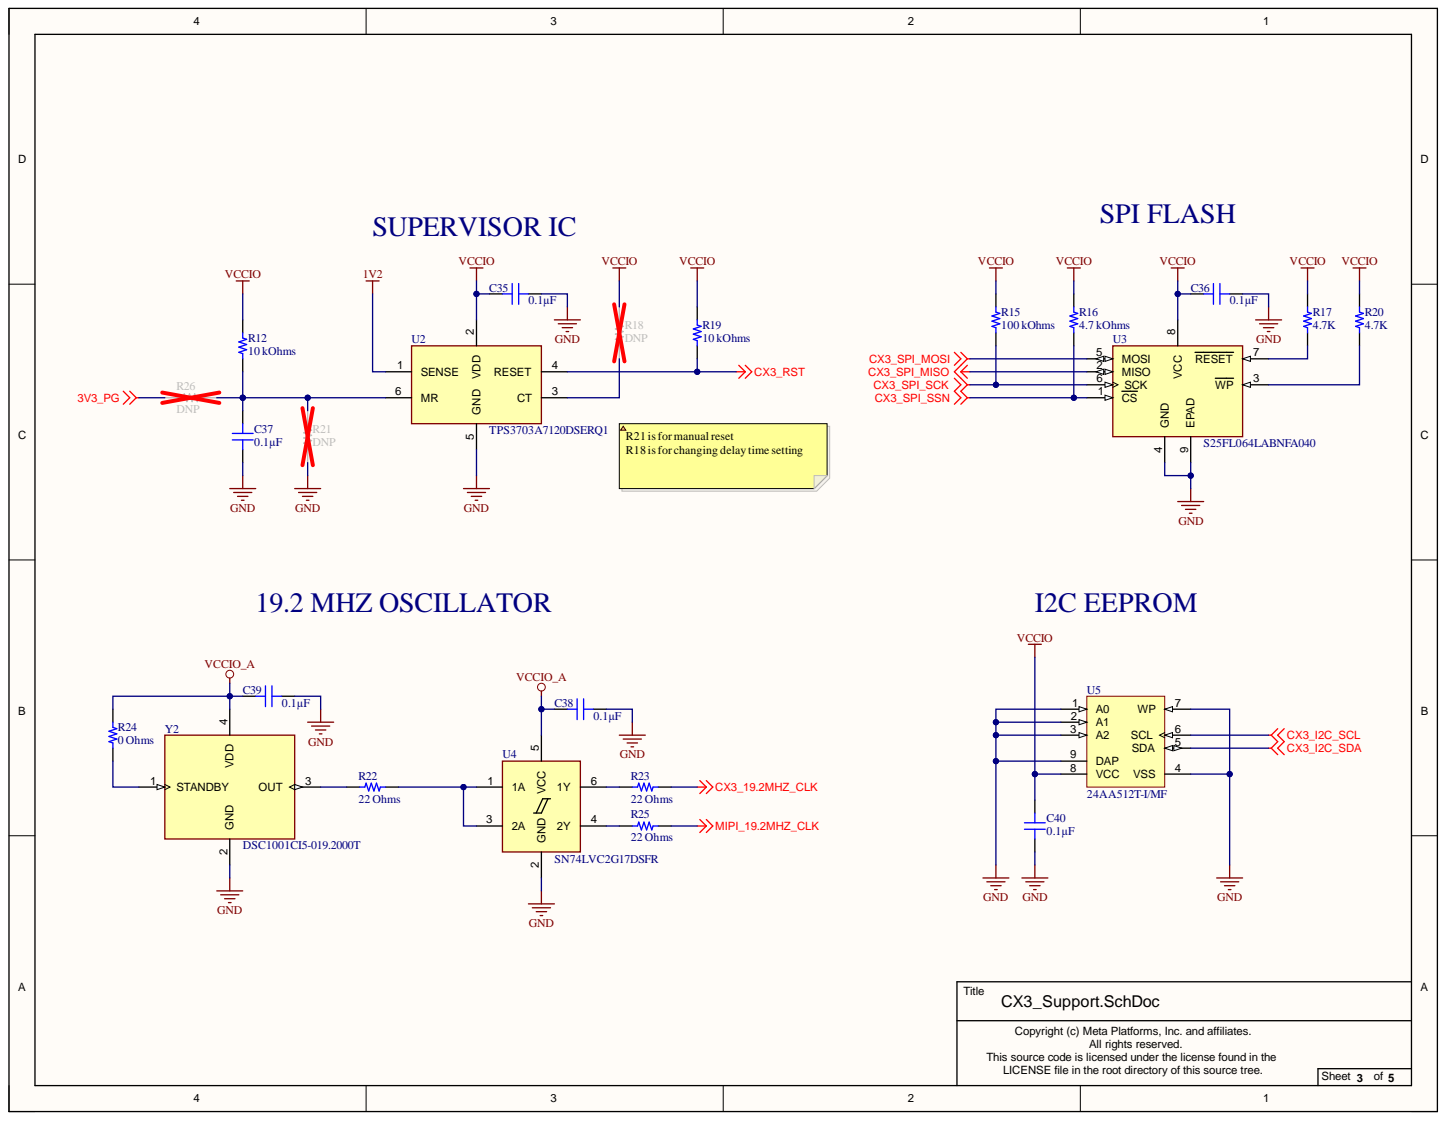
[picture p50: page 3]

SPI FLASH SUPERVISOR IC

R21 isfor manualreset
R18 isfor changing delay time setting

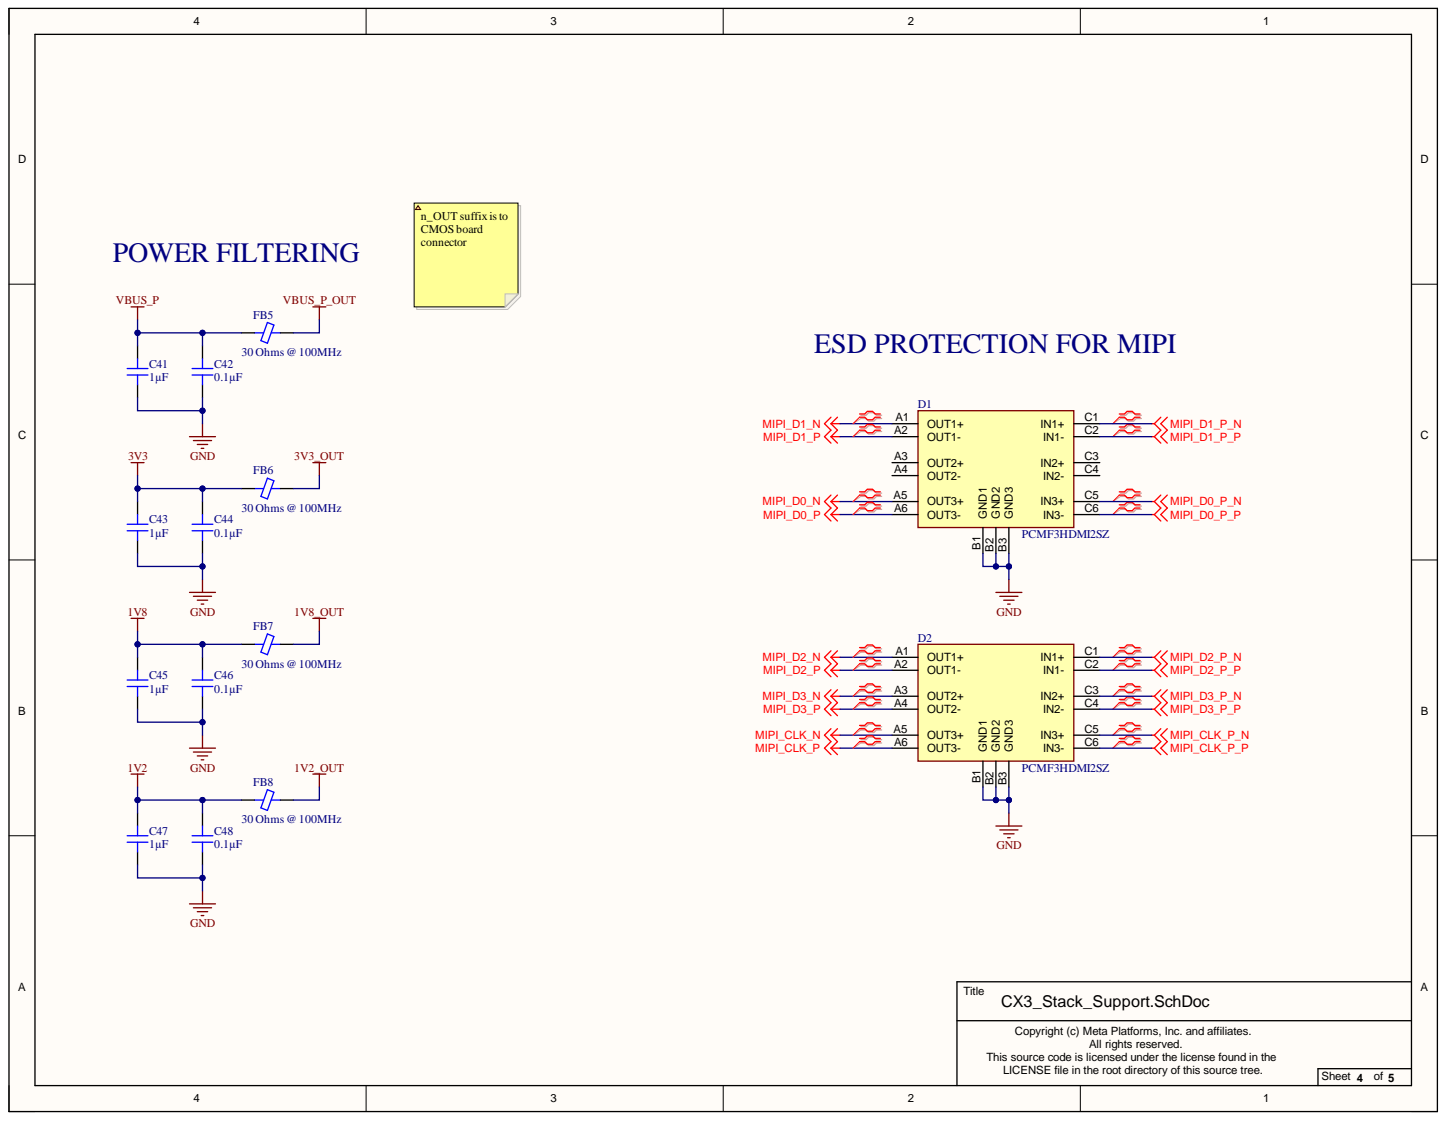
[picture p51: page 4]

ESD PROTECTION FOR MIPI

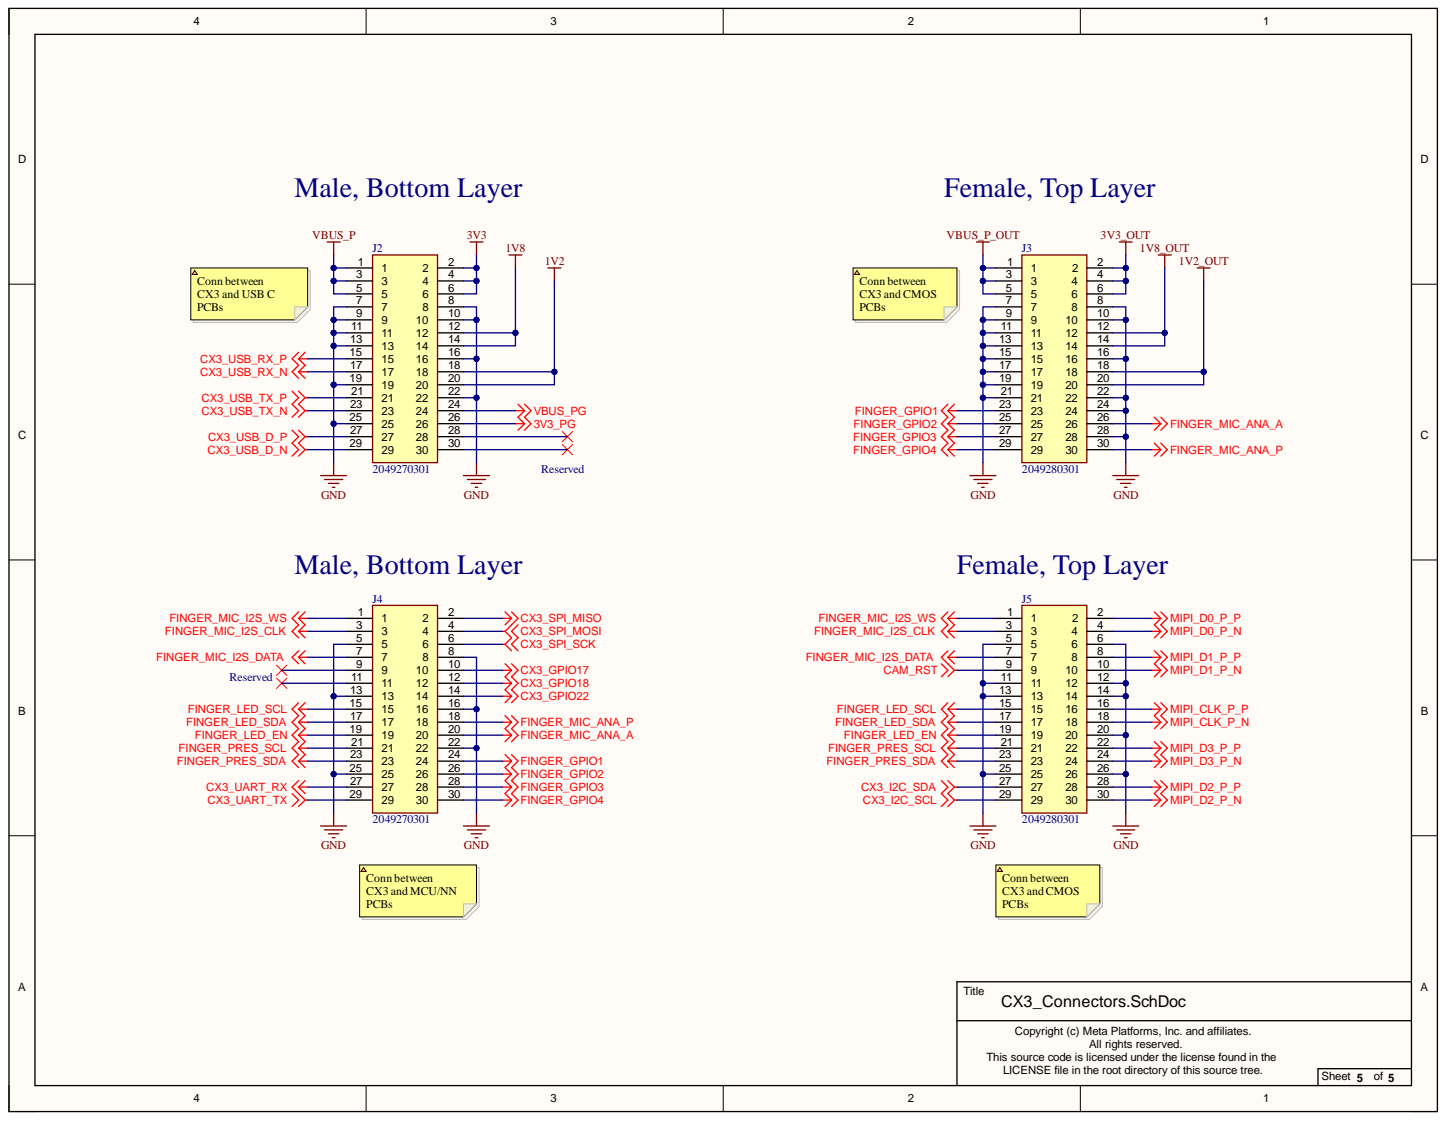
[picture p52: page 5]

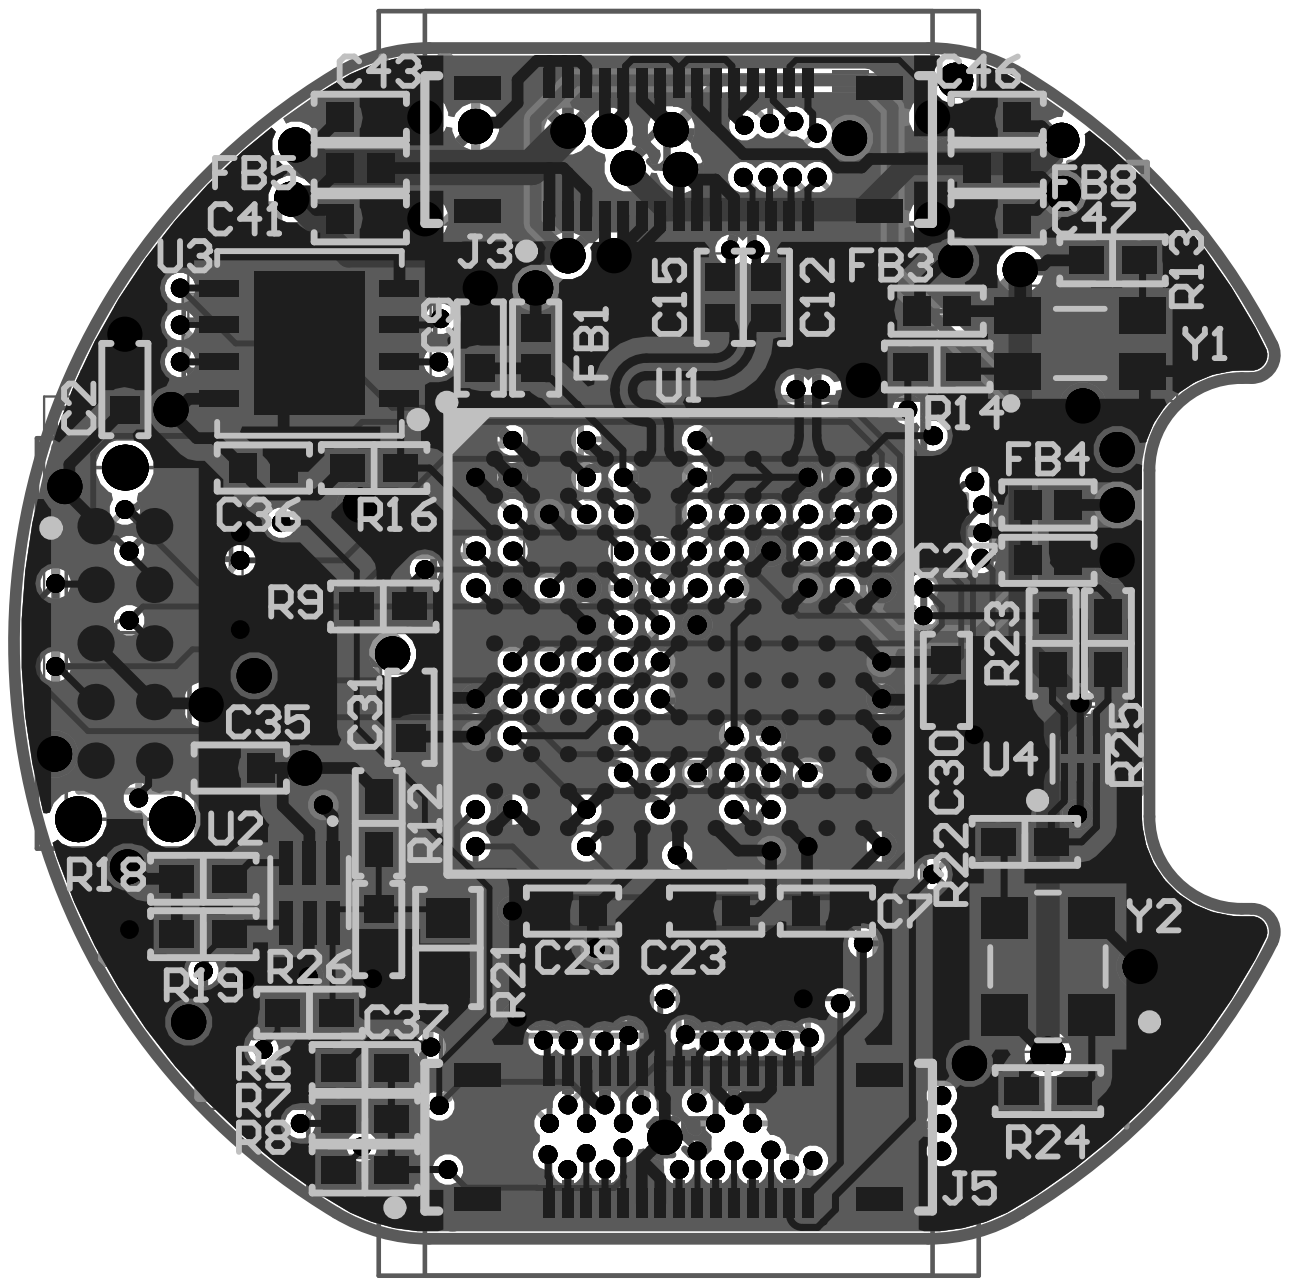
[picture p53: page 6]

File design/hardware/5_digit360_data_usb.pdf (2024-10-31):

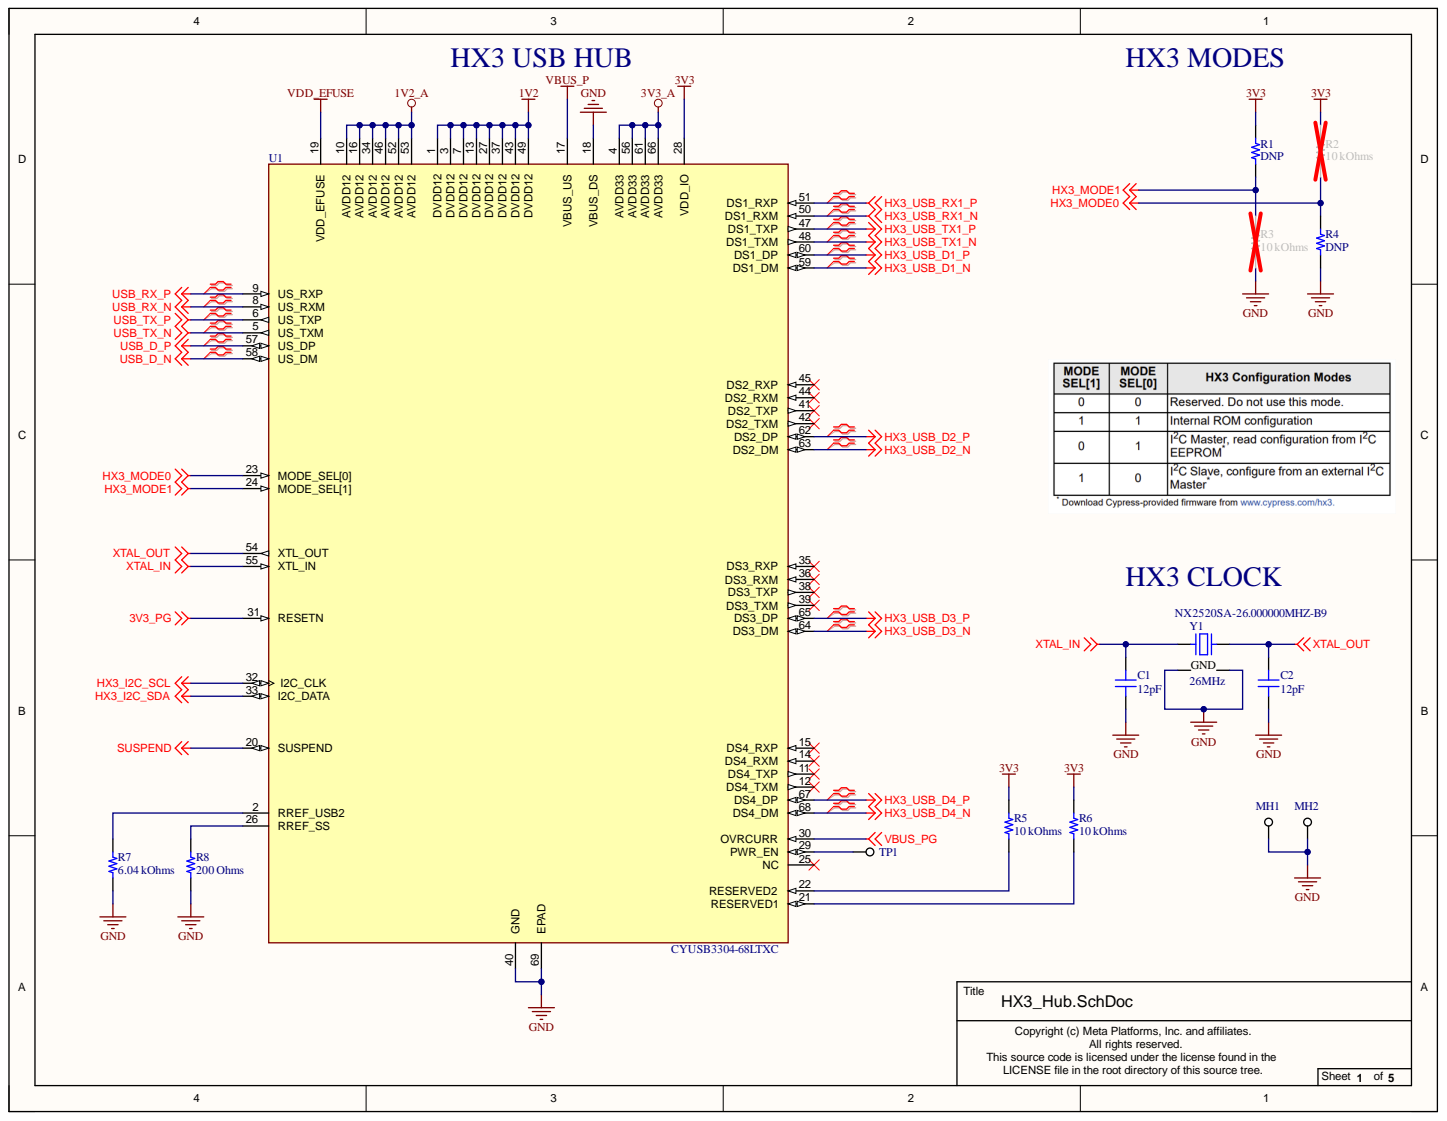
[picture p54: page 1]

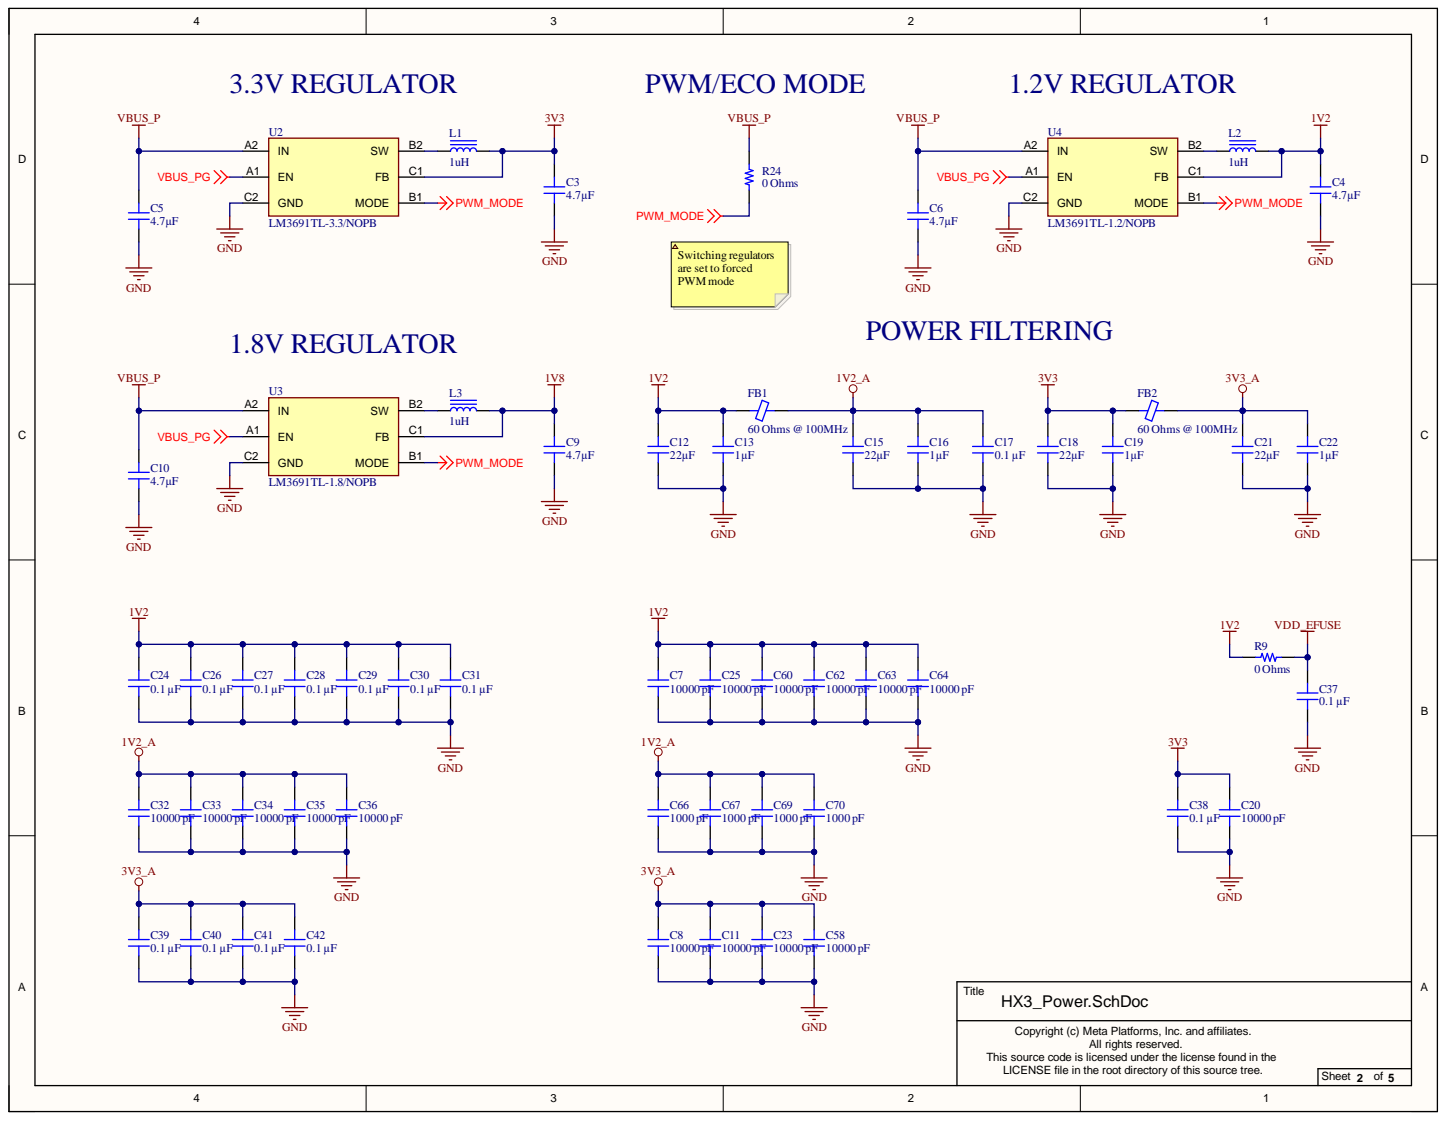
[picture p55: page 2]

Switching regulators
are set to forced
PWM mode

Copyright (c) Meta Platforms, Inc. and affiliates.

This source code is licensed under the license found in the
LICENSE file in the root directory of this source tree.

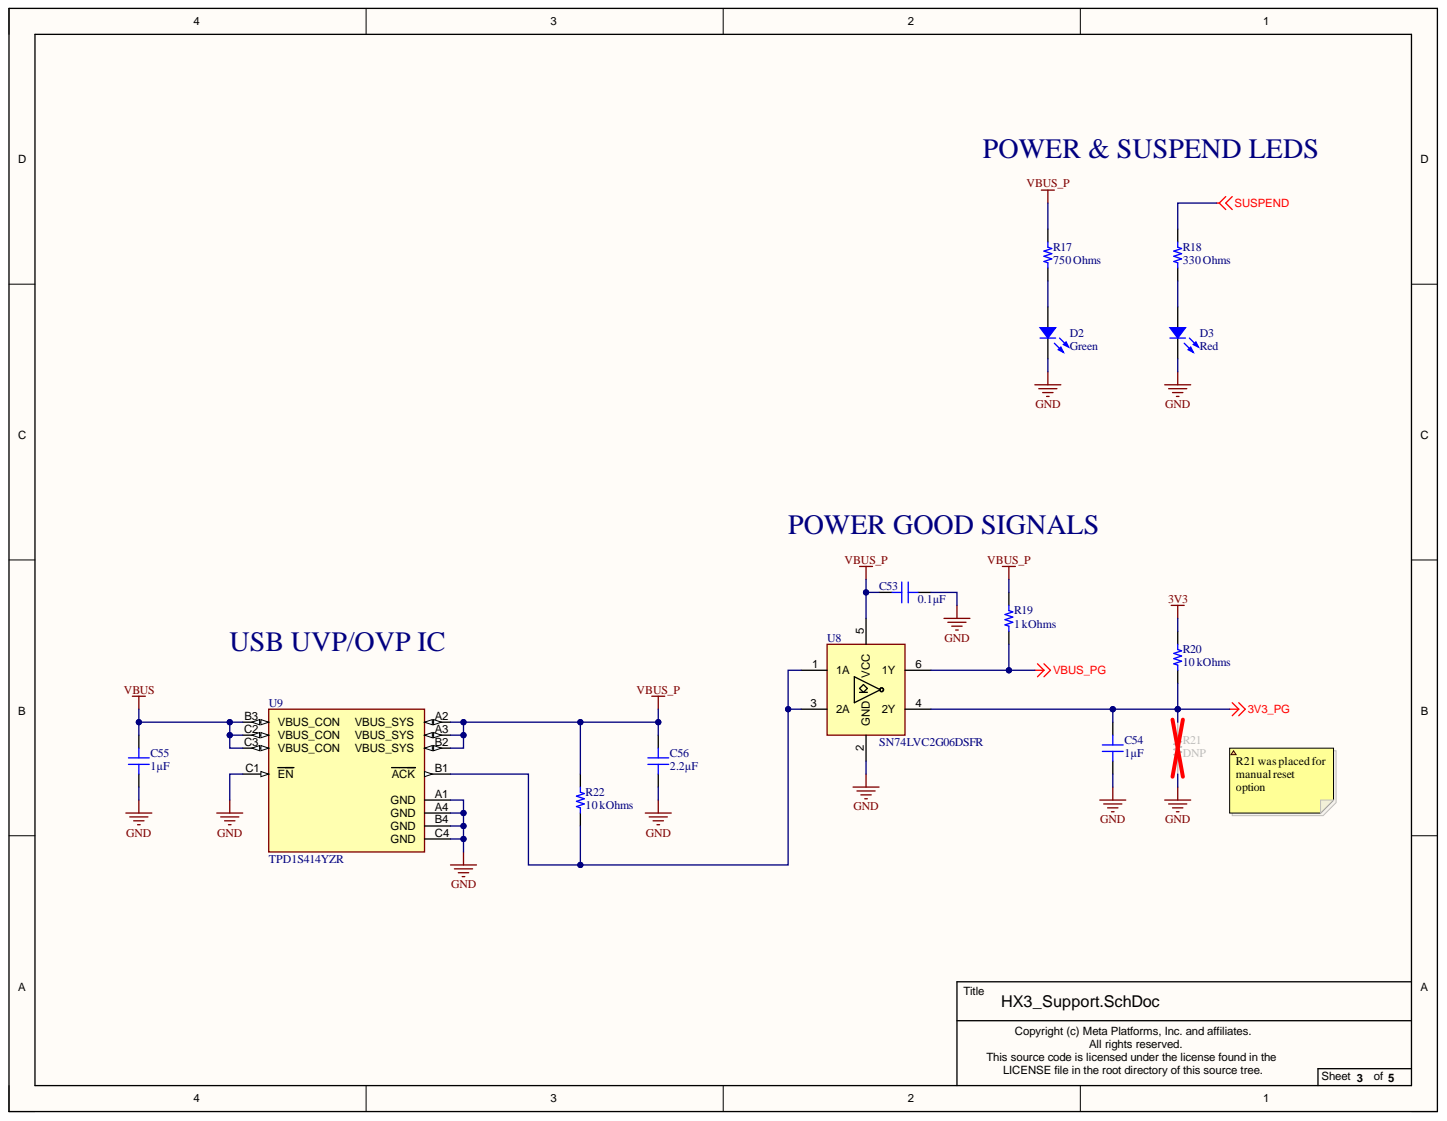
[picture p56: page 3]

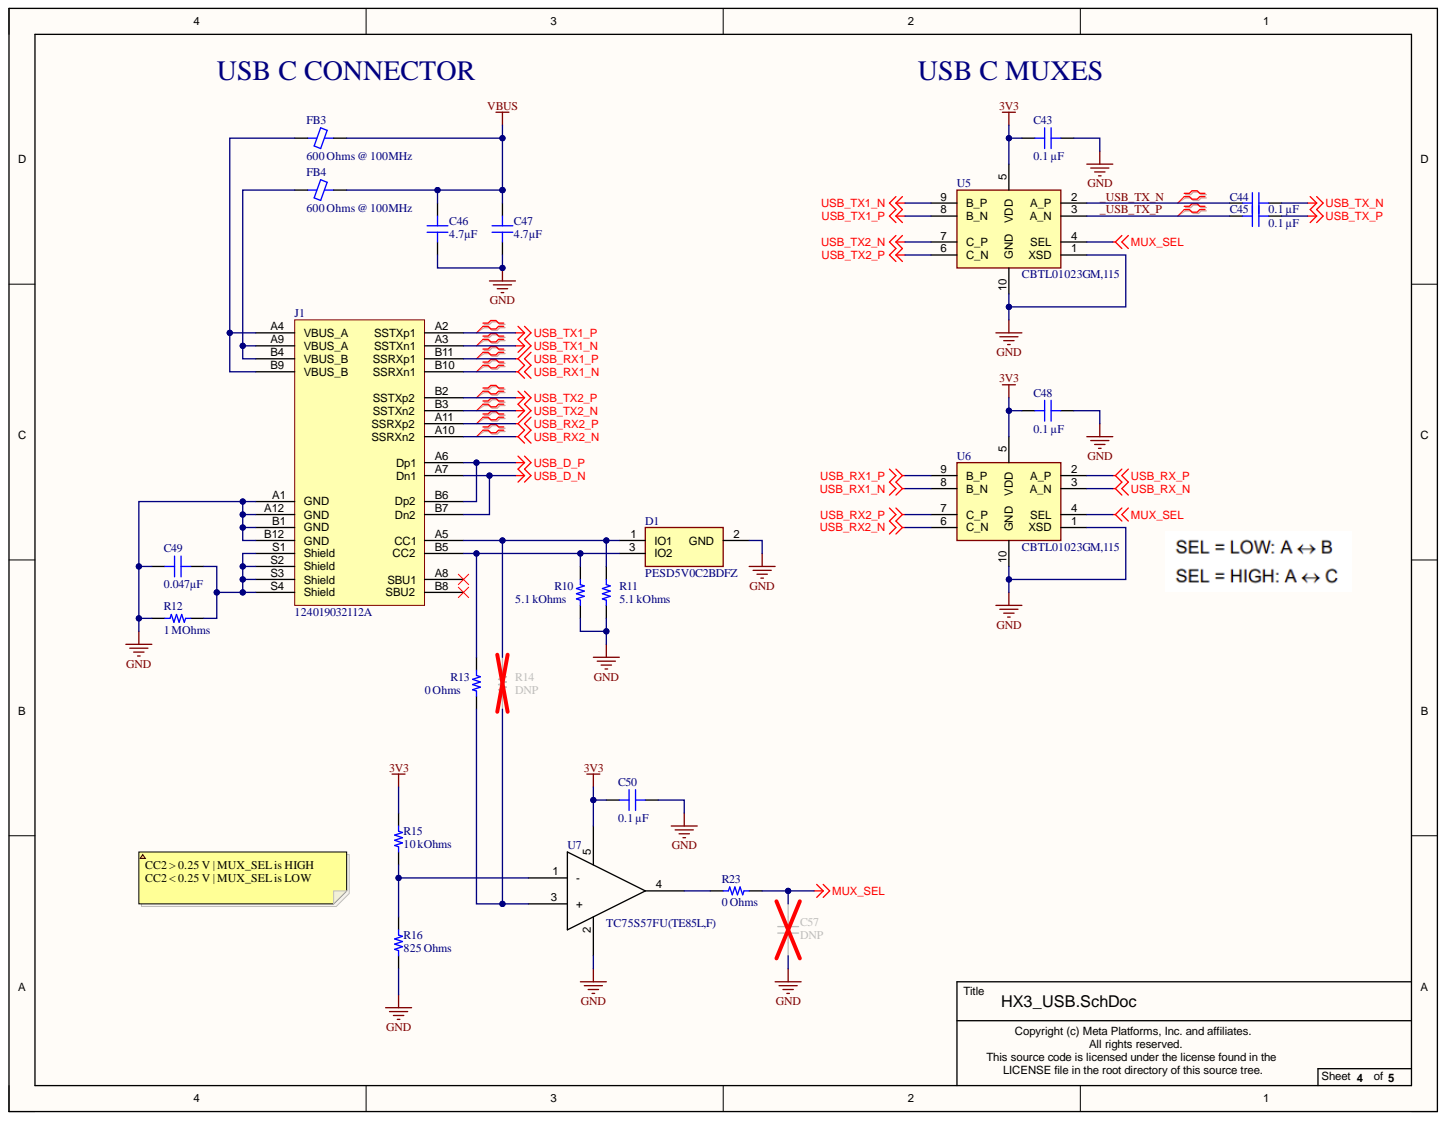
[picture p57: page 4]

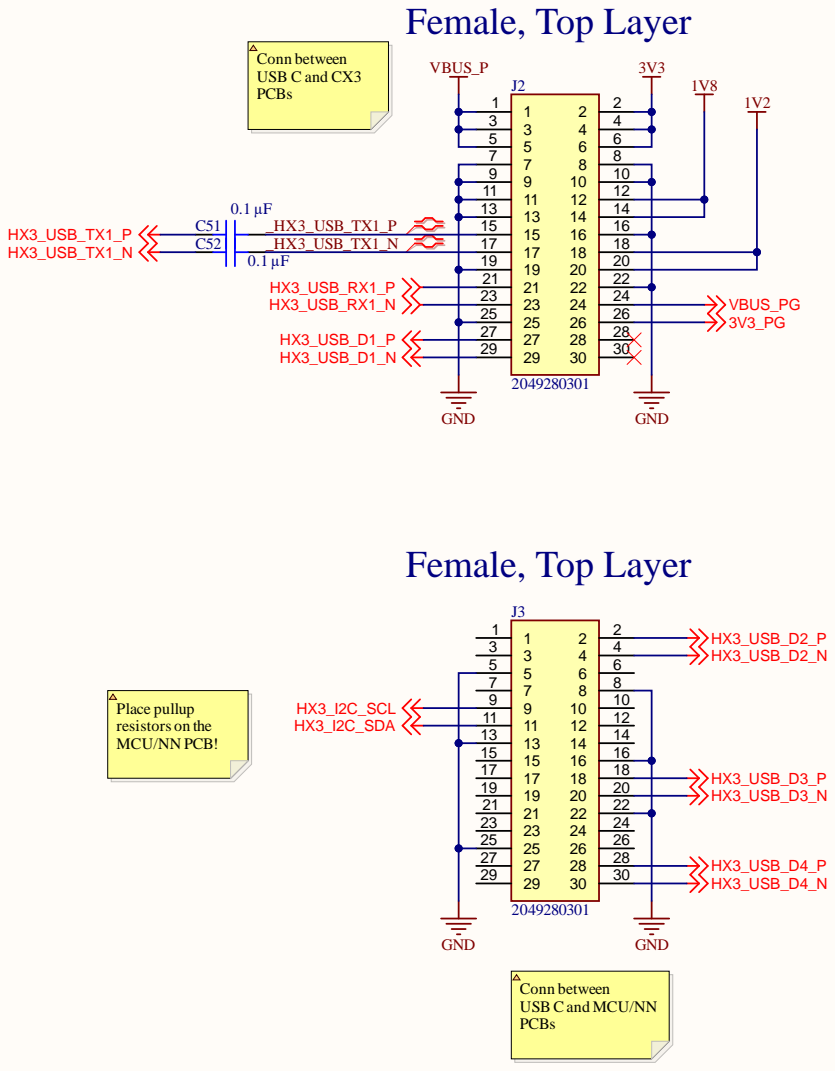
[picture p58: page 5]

_HX3_USB_TX1_N | 17 17

Conn between
USB C and MCU/NN
PCBs


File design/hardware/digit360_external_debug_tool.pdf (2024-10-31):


Copyright (c) Meta Platforms, Inc. and affiliates.

This source code is licensed under the license found in the
LICENSE file in the root directory of this source tree.


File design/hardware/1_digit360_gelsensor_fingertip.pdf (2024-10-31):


4 4
5 5
6 6
7 7

6 6 | I2S_WS
7 7 | I2S_CLK

I2S_DATA

Copyright (c) Meta Platforms, Inc. and affiliates.

This source code is licensed under the license found in the
LICENSE file in the root directory of this source tree.


VDDIO 4

SCX 1

Copyright (c) Meta Platforms, Inc. and affiliates.

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


1 9
2 0


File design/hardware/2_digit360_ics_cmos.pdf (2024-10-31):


A 1
B 1
A 7
A 8


RST L1 CLK M2 STANDBY K1

SMIPI_VSS C4

Copyright (c) Meta Platforms, Inc. and affiliates.

This source code is licensed under the license found in the
LICENSE file in the root directory of this source tree.





19 19
21 21


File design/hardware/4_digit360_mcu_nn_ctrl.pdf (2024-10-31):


Conn between
USB C and MCU/NN
PCBs

Copyright (c) Meta Platforms, Inc. and affiliates.

This source code is licensed under the license found in the
LICENSE file in the root directory of this source tree.


GPIO 2 from CMOS shutdown
GPIO 3,4 from CMOS shutter and flash

VDD D3
VDD F4
VDD F5
VDD F6
VDD F7





MCU_SPI_MOSI | | | BHI_SPI_MOSI
MCU_SPI_CLK | | | BHI_SPI_CLK

THREE-STATE 3




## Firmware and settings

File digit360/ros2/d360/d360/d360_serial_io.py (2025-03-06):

# Copyright (c) Meta Platforms, Inc. and affiliates.
# All rights reserved.

# This source code is licensed under the license found in the
# LICENSE file in the root directory of this source tree.


#!/usr/bin/env python3

from argparse import ArgumentParser
import betterproto
from cobs import cobs
import os
import rclpy.exceptions
import serial
import rclpy
import rclpy.qos
import rclpy.utilities
import rclpy.parameter
from typing import List, Tuple
import struct
from rclpy.node import Node
import numpy as np
from d360_msgs.msg import PressureD360, PressureAPD360, GasHTData, ImuRawD360, ImuEulerD360, ImuQuatD360
from builtin_interfaces.msg import Time
import time
from std_msgs.msg import Header
from rclpy.executors import MultiThreadedExecutor
from rcl_interfaces.msg import SetParametersResult
import warnings
from collections import deque
import yaml
from digit360.interface import proto as d360frame

class TimeDelta:
    def __init__(self, name: str) -> None:
        self.name:str  = name
        self.timestamps: deque= deque(maxlen=1000)
        self.count = 0
        self.report_freq = 1000
    
    def step(self, t_ms: float = None) -> None:
        if t_ms is None:
            t_ms = time.time()*1000
        self.timestamps.append(t_ms)
        if len(self.timestamps) == self.timestamps.maxlen:
            self.timestamps.popleft()

        self.count+=1

    def get_hz(self) -> float:
        delta = self.timestamps[-1] - self.timestamps[0]
        hz = 1000 * len(self.timestamps) / delta
        return hz
    
    def get_delta_stat(self) -> float:
        diff=np.diff(np.array(self.timestamps))
        mean = np.mean(diff)
        delta = np.std(diff)
        return mean, delta

    def report(self) -> str:
        return f"{self.name} Hz: {self.get_hz()}, mean/std: {self.get_delta_stat()} ms"
    
    def __call__(self, t_ms: float, silent:bool=False) -> str:
        "call this function periodically to have rate stats printed"
        self.step(t_ms)
        if self.count % self.report_freq == 0:
            msg=self.report()
            if not silent:
                print(msg)
            return msg
        return None

class Digit360():
    class ReadLine:
        def __init__(self, s):
            self.buf = bytearray()
            self.s = s
        
        def readline(self):
            i = self.buf.find(b"\x00")
            if i >= 0:
                r = self.buf[:i+1]
                self.buf = self.buf[i+1:]
                return r
            while True:
                i = max(1, min(2048, self.s.in_waiting))
                data = self.s.read(i)
                i = data.find(b"\x00")
                if i >= 0:
                    r = self.buf + data[:i+1]
                    self.buf[0:] = data[i+1:]
                    return r
                else:
                    self.buf.extend(data)    
    def __init__(self, port: str, port_timeout: float=1.0) -> None:
        self._dev = serial.Serial(port, timeout=port_timeout)
        self.overruns = 0
        self._device_buffer = bytearray()

        if not self._dev.is_open:
            raise IOError(f"Unable to access DIGIT360 data device at *{port}*!")
        self.readline = self.ReadLine(self._dev)

    def _read_device(self) -> bytearray:
        i = self._device_buffer.find(b"\x00")
        if i >= 0:
            r = self._device_buffer[: i + 1]
            self._device_buffer = self._device_buffer[i + 1 :]
            return r
        while True:
            i = max(1, min(2048, self._dev.in_waiting))
            data = self._dev.read(i)
            i = data.find(b"\x00")
            if i >= 0:
                r = self._device_buffer + data[: i + 1]
                self._device_buffer[0:] = data[i + 1 :]
                return r
            else:
                self._device_buffer.extend(data)

    def read(self) -> d360frame.Digit360Message:
        if self._dev.in_waiting > 4000:
            warnings.warn(f"DIGIT360 data serial buffer piling up {self._dev.in_waiting} bytes")
        data = self._read_device()
        if len(data) == 0:
            raise RuntimeError(f"DIGIT360 data serial port *{self._dev}* read timeout, wrong port?")
        data = self.decode(data)
        return data
    
    def decode(self, data: bytes) -> d360frame.Digit360Message:
        cobs_data = data.split(b"\x00")[0]
        digit360_frame = d360frame.Digit360Message()

        try:
            pb_data = cobs.decode(cobs_data)
            digit360_frame = digit360_frame.parse(pb_data)
        except cobs.DecodeError:
            self._dev.reset_input_buffer()
            warnings.warn("DIGIT360 Data::Decode::DecodeError cobs cannot be decoded")
        except IndexError:
            self.overruns += 1
            warnings.warn(f"DIGIT360 Data::Decode::IndexError, overrun {self.overruns}")
            self._dev.reset_input_buffer()
        except KeyError:
            self.overruns += 1
            warnings.warn(f"DIGIT360 Data::Decode::KeyError, overrun {self.overruns}")
            self._dev.reset_input_buffer()
        return digit360_frame
    
    def _send(self, data: bytes) -> None:
        self._dev.write(bytes(data))
        self._dev.flush()

    @property
    def is_open(self) -> bool:
        return self._dev.is_open

class D360Node(Node):
    def __init__(self) -> None:
        super().__init__('d360_node')

        self.n_led = 8

        # if there is a hydra parameter
        # Declare parameters for lighting control
        self.declare_parameters(
            namespace='',
            parameters=[
                ('port', '/dev/ttyACM0'),
                ("reliable_publisher", False),
                ("config_file", "default.yaml"),
                ("hand_config","default.yaml")
            ]
        )

        # Get the config file path from parameters
        config_file_path = self.get_parameter('config_file').get_parameter_value().string_value
        hand_config_path = self.get_parameter('hand_config').get_parameter_value().string_value
        
        print(f'DIGITG360 Node config file: {config_file_path}')
        print(f'DIGITG360 Node hand file: {hand_config_path}')

        if (lighting_params := self.load_lighting_params_from_yaml(hand_config_path)) is not None:
            self.lighting_params_from_yaml = lighting_params
            print(f"light loaded from hand config{self.lighting_params_from_yaml}")
        else:
            self.lighting_params_from_yaml = self.load_lighting_params_from_yaml(config_file_path)
            print(f"loaded from individual cfg path")

        # If YAML parameters exist and are complete, use them. Otherwise, use default values.
        if self.lighting_params_from_yaml:
            led_params = self.lighting_params_from_yaml
        else:
            led_params = self.get_default_led_params()

        self.declare_parameters(
            namespace="",
            parameters=[*led_params]
            )

        # lightcontrol dynamic param callback
        self.add_on_set_parameters_callback(self.check_param_updates)

        #  publishers for pressure, IMU, and gas data
        self.publisher_pressure = self.create_publisher(
            PressureD360, "pressure_topic", 1
        )
        self.publisher_imu_raw = self.create_publisher(ImuRawD360, "imu_raw_topic", 1)
        self.publisher_imu_euler = self.create_publisher(
            ImuEulerD360, "imu_euler_topic", 1
        )
        self.publisher_imu_quat = self.create_publisher(
            ImuQuatD360, "imu_quat_topic", 1
        )
        self.publisher_gas_hum_temp = self.create_publisher(GasHTData, "ght_topic", 1)

        if self.get_parameter("reliable_publisher").value:
            qos_reliable = rclpy.qos.QoSProfile(
                reliability=rclpy.qos.ReliabilityPolicy.BEST_EFFORT,
                history=rclpy.qos.HistoryPolicy.KEEP_ALL,
            )
            self.publisher_pressure_ap = self.create_publisher(
                PressureAPD360, "pressure_ap_topic", qos_profile=qos_reliable
            )
        else:
            self.publisher_pressure_ap = self.create_publisher(
                PressureAPD360, "pressure_ap_topic", 1
            )

        self.publisher_pressure_ap_seq = 0

        self.digit360 = Digit360(self.get_parameter("port").value)

        self.parameter_dirty = True
        self.timer_pressure_ap = TimeDelta("pressure_ap")


    def load_lighting_params_from_yaml(self, config_file: str) -> List[Tuple[str, int]]:
        if os.path.exists(config_file):
            with open(config_file, 'r') as file:
                yaml_config = yaml.safe_load(file)

            # Navigate to the 'lighting' section inside 'params'
            if 'params' in yaml_config and 'lighting' in yaml_config['params']:
                lighting_config = yaml_config['params']['lighting']
                
                # Define all required lighting parameter keys
                required_lighting_params = [
                    'lighting_alpha',
                    'lighting_1_r', 'lighting_1_g', 'lighting_1_b',
                    'lighting_2_r', 'lighting_2_g', 'lighting_2_b',
                    'lighting_3_r', 'lighting_3_g', 'lighting_3_b',
                    'lighting_4_r', 'lighting_4_g', 'lighting_4_b',
                    'lighting_5_r', 'lighting_5_g', 'lighting_5_b',
                    'lighting_6_r', 'lighting_6_g', 'lighting_6_b',
                    'lighting_7_r', 'lighting_7_g', 'lighting_7_b',
                    'lighting_8_r', 'lighting_8_g', 'lighting_8_b'
                ]
                # Check if all required lighting parameters exist in the YAML config
                missing_params = [param for param in required_lighting_params if param not in lighting_config]

                if missing_params:
                    self.get_logger().warn(f"Missing lighting parameters: {missing_params}")
                    return None  # Indicate that parameters are incomplete
                else:
                    # Return parameters from YAML
                    return [(key, lighting_config[key]) for key in required_lighting_params]
            else:
                self.get_logger().warn(f"Lighting parameters not found in the config file.{config_file}")
                return None

        else:
            self.get_logger().warn(f"Config file {config_file} does not exist.")
            return None


    def get_default_led_params(self):
        """
        Get default lighting parameters if no YAML file is provided.
        """
        print(f" loading default light params - NO LIGHTING PARAMS FROM config file")
        led_params = []
        led_params.append((f'lighting_alpha', 255))
        for ch in range(1, self.n_led + 1):
            led_params.append((f'lighting_{ch}_r', int(ch % 3 == 0) * 15))
            led_params.append((f'lighting_{ch}_g', int(ch % 3 == 1) * 15))
            led_params.append((f'lighting_{ch}_b', int(ch % 3 == 2) * 15))
        return led_params

    def check_param_updates(
        self, parameters: List[rclpy.parameter.Parameter]
    ) -> SetParametersResult:
        result = SetParametersResult(successful=True)
        for p in parameters:
            if p.name == "port":
                result.successful = False
                result.reason = (
                    "port cannot be dynamically changed, please restart the node"
                )
                return result
            if p.name.startswith("lighting_"):
                if p.type_ != p.Type.INTEGER:
                    result.successful = False
                    result.reason = "lighting value must be an integer"
                    return result

        self.parameter_dirty = True
        return result

    def update_lighting_parameters(self) -> None:
        """
        Update lighting parameters and write them to the Digit360 device.
        """
        new_lighting_alpha = self.get_parameter(f'lighting_alpha').value
        for ch in range(1, self.n_led+1):
            new_lighting_r = self.get_parameter(f'lighting_{ch}_r').value
            new_lighting_g = self.get_parameter(f'lighting_{ch}_g').value
            new_lighting_b = self.get_parameter(f'lighting_{ch}_b').value
            # Write light values to Digit360 using the function
            self.write_lighting_to_digit360(new_lighting_alpha, ch, new_lighting_r, new_lighting_g, new_lighting_b)

    def write_lighting_to_digit360(self, alpha: int, channel:int, r:int, g:int, b:int) -> None:
        """
        Write lighting values to Digit360 device.
        """
        # Form a protobuf message for lighting
        lighting_msg = d360frame.LightingControl()
        lighting_msg.alpha = alpha
        lighting_msg.channel = d360frame.LightingChannel(channel)
        lighting_msg.r = r
        lighting_msg.g = g
        lighting_msg.b = b

        message = d360frame.Digit360Message(lighting_control=lighting_msg)
        # Write the lighting data to the Digit360 device
        self.get_logger().info(f"send {message}")
        self.digit360._send(message)

    def process_pressure_data(self, data:d360frame.PressureData) -> None:
        pressure_msg = PressureD360()
        time_pressure_msg = Time()

        # Assign data to the header - ros time
        pressure_msg.header.stamp = self.get_clock().now().to_msg()
        pressure_msg.header.frame_id = "D360"

        # Create and publish pressure message
        pressure_msg.ts = data.pressure_data.ts
        pressure_msg.pressure = data.pressure_data.pressure
        pressure_msg.temperature = data.pressure_data.temperature

        self.publisher_pressure.publish(pressure_msg)

    def process_pressure_ap_data(self, data:d360frame.PressureApData) -> None:
        channel_a = data.pressure_ap_data.channel_a
        channel_b = data.pressure_ap_data.channel_b

        pres_ap_msg = PressureAPD360()
        pres_ap_msg.seq = self.publisher_pressure_ap_seq
        self.publisher_pressure_ap_seq += 1
        
        # Assign data to the header - ros time
        pres_ap_msg.header.stamp = self.get_clock().now().to_msg()
        pres_ap_msg.header.frame_id = "D360"

        # Device time
        pres_ap_msg.ts = data.pressure_ap_data.ts
        
        pres_ap_msg.ch_a.extend(np.frombuffer(channel_a, dtype=np.uint16))
        pres_ap_msg.ch_b.extend(np.frombuffer(channel_b, dtype=np.uint16))
        self.publisher_pressure_ap.publish(pres_ap_msg)

    def process_imu_raw_data(self, data:d360frame.ImuData) -> None:
        imu_msg = ImuRawD360()

        # Assign data to the header - ros time
        imu_msg.header.stamp = self.get_clock().now().to_msg()
        imu_msg.header.frame_id = "D360"
        
        # Device time
        imu_msg.ts = data.imu_data.ts
        
        # Sensor time
        imu_msg.sensor_ts = data.imu_data.raw.ts_ght
        
        imu_msg.type = data.imu_data.raw.sensor
        imu_msg.x = data.imu_data.raw.x
        imu_msg.y = data.imu_data.raw.y
        imu_msg.z = data.imu_data.raw.z

        self.publisher_imu_raw.publish(imu_msg)

    def process_imu_euler_data(self, data:d360frame.ImuData) -> None:
        imu_msg = ImuEulerD360()

        # Assign data to the header - ros time
        imu_msg.header.stamp = self.get_clock().now().to_msg()
        imu_msg.header.frame_id = "D360"

        # Device time
        imu_msg.ts = data.imu_data.ts
        
        # Sensor time
        imu_msg.sensor_ts = data.imu_data.euler.ts_ght
        imu_msg.heading = data.imu_data.euler.heading
        imu_msg.pitch = data.imu_data.euler.pitch
        imu_msg.roll = data.imu_data.euler.roll

        self.publisher_imu_euler.publish(imu_msg)

    def process_imu_quat_data(self, data:d360frame.ImuData) -> None:
        imu_msg = ImuQuatD360()

        # Assign data to the header - ros time
        imu_msg.header.stamp = self.get_clock().now().to_msg()
        imu_msg.header.frame_id = "D360"

        # Device time
        imu_msg.ts = data.imu_data.ts

        # Sensor time
        imu_msg.sensor_ts = data.imu_data.quat.ts_ght
        imu_msg.quat.x = data.imu_data.quat.x
        imu_msg.quat.y = data.imu_data.quat.y
        imu_msg.quat.z = data.imu_data.quat.z
        imu_msg.quat.w = data.imu_data.quat.w
        imu_msg.accuracy = data.imu_data.quat.accuracy

        self.publisher_imu_quat.publish(imu_msg)

    def process_gasht_data(self, data:d360frame.GasHtData) -> None:
        ght_msg = GasHTData()
        
        # Assign data to the header - ros time
        ght_msg.header.stamp = self.get_clock().now().to_msg()
        ght_msg.header.frame_id = "D360"

        # Device time
        ght_msg.ts = data.gasht_data.ts

        # Sensor time
        ght_msg.sensor_ts = data.gasht_data.ts_ght
        
        ght_msg.temperature = data.gasht_data.temperature
        ght_msg.pressure = data.gasht_data.pressure
        ght_msg.humidity = data.gasht_data.humidity
        ght_msg.gas = data.gasht_data.gas
        ght_msg.gas_index = int(data.gasht_data.gas_index)

        self.publisher_gas_hum_temp.publish(ght_msg)

    def process_data(self, data:d360frame.Digit360Message) -> None:
        frame_name, frame_type = betterproto.which_one_of(data, "type")
        if isinstance(frame_type, d360frame.PressureData):
            self.process_pressure_data(data)
        elif isinstance(frame_type, d360frame.PressureApData):
            msg = self.timer_pressure_ap(data.pressure_ap_data.ts, silent=True)
            if msg:
                self.get_logger().info(msg)
            self.process_pressure_ap_data(data)
        elif isinstance(frame_type, d360frame.ImuData):
            sensor_name, sensor_type = betterproto.which_one_of(data.imu_data, "imu_type")
            if isinstance(sensor_type, d360frame.RawImuData):
                self.process_imu_raw_data(data)
            elif isinstance(sensor_type, d360frame.EulerData):
                self.process_imu_euler_data(data)
            elif isinstance(sensor_type, d360frame.QuatData):
                self.process_imu_quat_data(data)
            else:
                self.get_logger().warn(f"not implemented imu sensor type {sensor_type}")
        elif isinstance(frame_type, d360frame.GasHtData):
            self.process_gasht_data(data)

    def fake_run(self) -> None:
        while True:
            data = d360frame.Digit360Message(pressure_ap_data=d360frame.PressureApData(channel_a=b'1'*1000, channel_b=b'2'*1000))
            self.process_data(data)
            time.sleep(0.001)

    def run(self) -> None:
        try:
            while rclpy.ok():  # Continuously loop until ROS is shutdown
                try:
                    with warnings.catch_warnings(record=True) as warnings_list:
                        data = self.digit360.read()
                    for w in warnings_list:
                        self.get_logger().warn(f'{os.path.basename(w.filename)}:{w.lineno} {w.message}', throttle_duration_sec=1, skip_first=1)

                    self.process_data(data)
                except (struct.error, ValueError, AssertionError) as e:
                    # decoding error in first second
                    self.get_logger().warn(str(e), throttle_duration_sec=1, skip_first=1)

                if self.parameter_dirty:
                    self.update_lighting_parameters()
                    self.parameter_dirty=False

        except (KeyboardInterrupt, rclpy.exceptions.InvalidHandle) as e:
            pass

def main(rawargs:list=None) -> None:
    rclpy.init(args=rawargs)
    stripped_args = rclpy.utilities.remove_ros_args(rawargs)
    parser = ArgumentParser()
    parser.add_argument("--fake", action="store_true", help="Run in test fake data mode")
    args = parser.parse_args(args=stripped_args[1:])
    node = D360Node()
    
    e = MultiThreadedExecutor()

    e.add_node(node)
    if args.fake:
        future=e.create_task(node.fake_run)
    else:
        future=e.create_task(node.run)
    try:
        e.spin_until_future_complete(future)
        future.result()
    except KeyboardInterrupt:
        pass
    
    node.destroy_node()
    rclpy.try_shutdown()


if __name__ == '__main__':
    main()

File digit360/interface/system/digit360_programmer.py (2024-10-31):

# Copyright (c) Meta Platforms, Inc. and affiliates.
# All rights reserved.

# This source code is licensed under the license found in the
# LICENSE file in the root directory of this source tree.

import argparse
import os
import subprocess
import sys
import time
from typing import Any
import proto as d360frame
import pyudev
import serial
from digit360.interface.digit360 import Digit360

DFU_MINIMUM_VERSION = 0.10
SCRIPT_DIR = os.path.dirname(__file__)
DFU_PATH = os.path.join(SCRIPT_DIR, "firmware/dfu-util/")
DFU_UTIL = f"{DFU_PATH}/dfu-util"
D360_FLASH_START_ADDR = 0x08000000

def firmware_update(fw_bin_file: str) -> None:
    fw_cmd = "{0} -d 0483:df11 -a 0 --dfuse-address {1}:leave -R -D {2}".format(
        DFU_UTIL, D360_FLASH_START_ADDR, fw_bin_file
    )
    os.system(fw_cmd)


def check_dfu_util_version() -> None:
    try:
        p = subprocess.Popen(
            [DFU_UTIL, "-V"], stdout=subprocess.PIPE, stderr=subprocess.PIPE
        )
        output = p.stdout.read()
    except Exception as e:
        print(f"Cannot find dfu-util, {e}")
        sys.exit()

    _dfu_ver = str(output).split("\\n")[0].split("dfu-util")[1].strip()
    dfu_ver = float(_dfu_ver.split("-")[0])

    if dfu_ver < DFU_MINIMUM_VERSION:
        print(f"dfu-util version greater than {DFU_MINIMUM_VERSION} required!")
        sys.exit()


def is_device_dfu_ready() -> int:
    context = pyudev.Context()
    devices = context.list_devices(subsystem="usb", find_all=True).match_property(
        "ID_VENDOR_ID", "0483"
    )
    return len(list(devices))


def main(args: argparse.Namespace) -> None:
    check_dfu_util_version()

    print(f"Connecting to device at {args.device}...")
    try:
        d360 = Digit360(args.device)
    except Exception as e:
        print(e)
        print(
            "Cannot connect to device, make sure any threads accessing device are closed."
        )
        sys.exit()

    system_msg = d360frame.SystemData()
    system_msg.version_major = 0xFF

    msg = d360frame.Digit360Message(system_data=system_msg)

    d360.send(msg)

    while d360.is_open and not is_device_dfu_ready():
        print("Trying to enter DFU mode...")
        try:
            d360.send(msg)
        except Exception:
            pass
        time.sleep(0.5)

    print("DFU mode ready!")
    firmware_update(args.fw)
    print("Finished downloading firmware!")


if __name__ == "__main__":
    parser = argparse.ArgumentParser(description="DIGIT360 Firmware Update Utility")
    parser.add_argument("device", type=str, help="DIGIT360 tty device")
    parser.add_argument("fw", type=str, help="Firmware binary file")

    args = parser.parse_args()
    main(args)

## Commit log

2025-01-07 updated led setup to fix the bug and enable lights (#5)
2025-03-06 Update d360_serial_io.py
    readline error solved
    [d360_serial_io.py]
2025-03-06 Update digit360.py
    resolved - import proto error
    [digit360.py]
